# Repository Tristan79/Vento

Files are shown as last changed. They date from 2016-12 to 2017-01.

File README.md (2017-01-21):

# Vento

Wanna control you ventilation unit from your computer, tablet or phone? Can't sleep? Cuz the noise of the ventilation unit is too loud! Can't replace the unit because it is not yours, add Vento! The itho, duco, orcon, zehnder, storkair, berschenhoek: Arduino [MySensors 2.0](https://www.mysensors.org) perilex ventilation controller!

Manufactures air ventilation unit: itho, duco, orcon, zehnder, storkair, berschenhoek or ...

Price range parts: essential € 5 ~ full blown € 50

You need a MySensors gateway and a Smart Home Controller supporting MySensors like [Domoticz](www.domoticz.com)
Luckily if you have a raspberry Pi a gateway costs just 67 cents extra! [See this](https://www.domoticz.com/forum/viewtopic.php?t=14365&#p105148)

Contact <tristan@monkeycat.nl>!

## WARNING!

READ THE LICENSE FIRST! BE CAREFULL! 

## Other Nice Smarthome stuff!!

 * [iBrew](https://github.com/Tristan79/iBrew) iKettle, iKettle 2.0 and Smarter Coffee Interface
 * [iSamsungTV](https://github.com/Tristan79/iSamsungTV) the command line interface to Samsung TV series C, D, E, F and Blue Ray Disc Players with Smart Hub feature.
 * [Medisana Scale](https://github.com/keptenkurk/BS440) with [Domoticz](http://domoticz.com/) bridge to Medisana BS440, BS430,... weight scales.
 * [Xiaomi Mi Plant Sensor](https://github.com/Tristan79/miflora) with [Domoticz](http://domoticz.com/) bridge
 * [HUE Hack](https://github.com/Tristan79/HUEHack) Soft Link Button for HUE Bridge (& rooting the bridge & enable WiFi!)

## Vento!

Domoticz

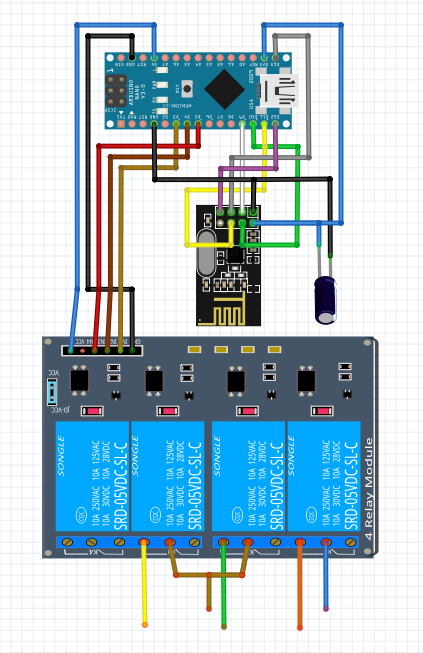
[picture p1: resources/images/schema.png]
Scheme3


Choose between Vento L1 and Vento L3 depending on your model.

## Vento L1

__Make sure your unit has the following specification__

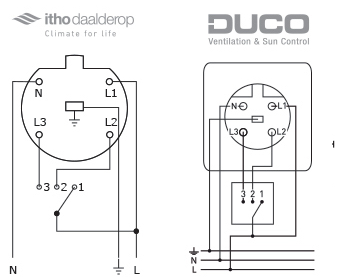
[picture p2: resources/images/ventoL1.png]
Specs2


You can cut open the existing cable and use that! Or use extra perilex plugs!

 * Blue: N power socket
 * Brown: L1 power socket
 * Orange: N ventilation unit
 * Yellow: L3 ventilation unit
 * Green: L2 ventilation unit
 * L2 & L3 power socket terminated
 * L1 & Ground directly connected

```
Power Socket          Ventilation Unit
Ground ________________________ Ground
N  ____________ Relay 1 ____________ N
L1 ________________________________ L1
L2 (T)      |___Relay 2 ___________ L2
L3 (T)      |__ Relay 3 ___________ L3
```

## Vento L3
__Make sure your unit has the following specification__

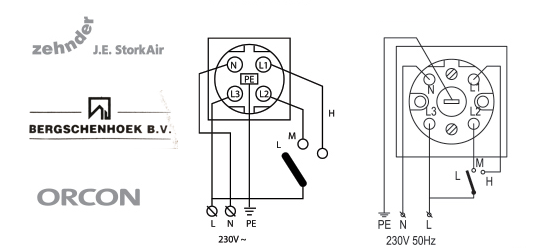
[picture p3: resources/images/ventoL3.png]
Specs3


You can cut open the existing cable and use that! Or use extra perilex plugs!

 * Blue: N power socket
 * Brown: L3 power socket
 * Orange: N ventilation unit
 * Yellow: L1 ventilation unit
 * Green: L2 ventilation unit
 * L1 & L2 power socket terminated
 * L3 & Ground directly connected

```
Power Socket          Ventilation Unit
Ground ________________________ Ground
N  ____________ Relay 1 ____________ N
L3 ________________________________ L3
L2 (T)      |___Relay 2 ___________ L2
L1 (T)      |__ Relay 3 ___________ L1
```

## Relay

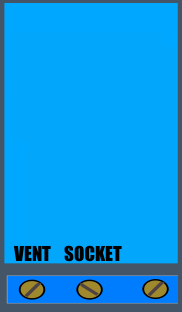
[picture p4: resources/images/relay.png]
Relay


## [Domoticz](www.domoticz.com)

## Showcase

Prototype!?

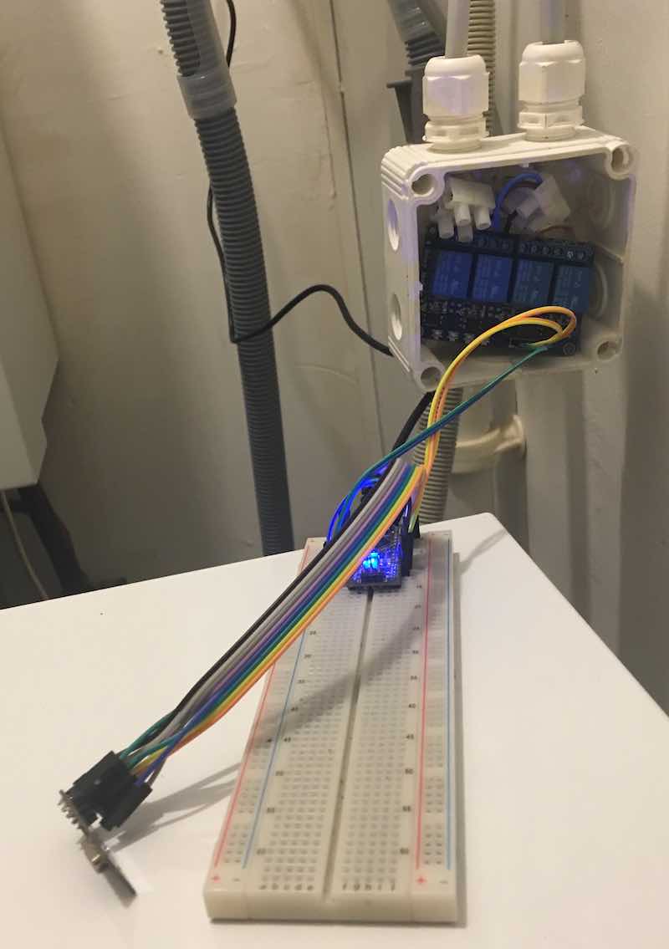
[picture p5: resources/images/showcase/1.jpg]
Showcase1


The unit...

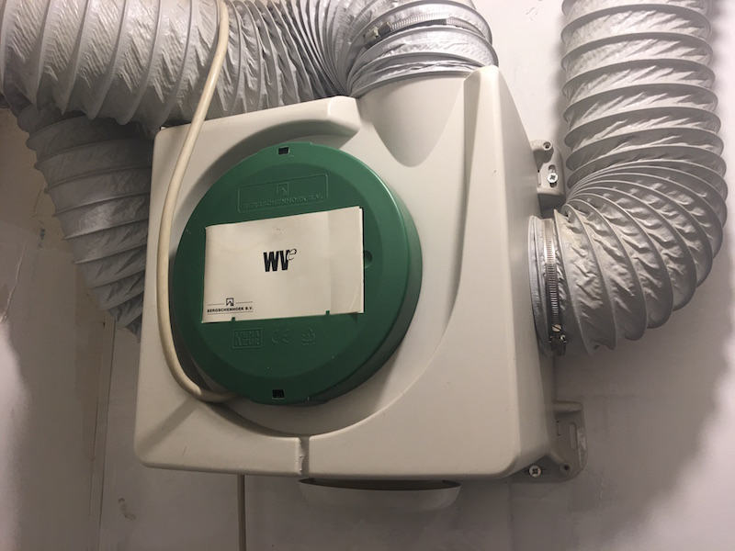
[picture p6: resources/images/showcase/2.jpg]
Showcase2


All connected!

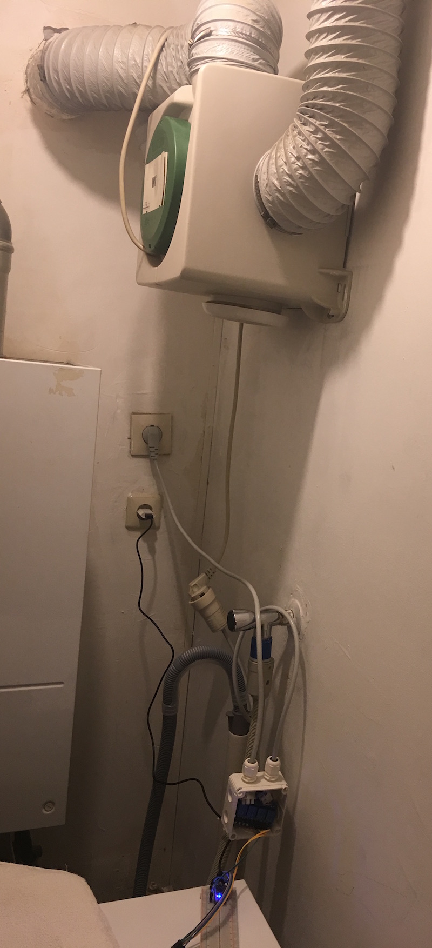
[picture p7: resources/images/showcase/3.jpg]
Showcase3


Assembled!

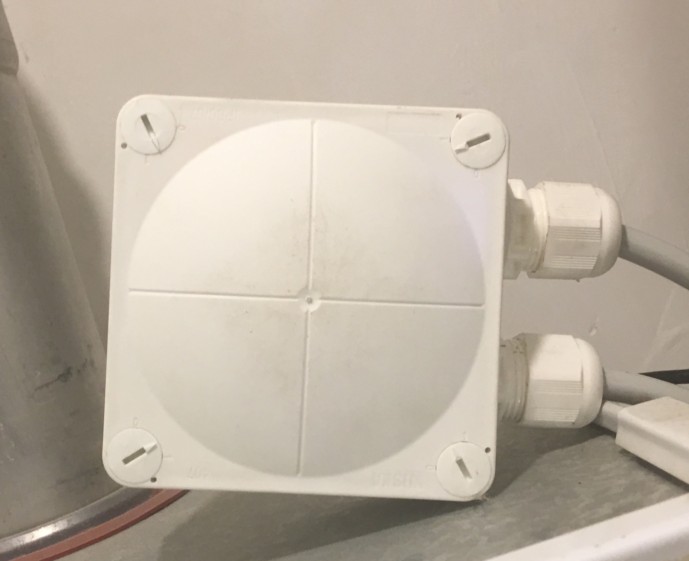
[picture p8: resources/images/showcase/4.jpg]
Showcase4


Photo's in the dark such that you really see the lights of Level 1, Level 2 and Level 3

Level1Level2Level3

## WARNING

Make sure you seperate the 5v wires and circuits from the 220v wires! That if one comes loose it will not touch any 5v stuff and burn the unit! I glued in a plastic seperator dividing the high wires and the rest of the stuff... 
 
## Parts, Shop & Prices 

Prices are snapshot 27 december 2016:

__Essential__
 * € 1.72 [Relay 4x](https://nl.aliexpress.com/item/1pcs-lot-4-channel-relay-module-4-channel-relay-control-board-with-optocoupler-Relay-Output-4/32325541816.html)
 * € 2.42 [Arduino Nano v3 ATmega328](https://nl.aliexpress.com/item/Free-Shipping-1PCS-LOT-For-arduino-Nano-3-0-Atmel-ATmega328-Mini-USB-Board/32773364249.html)
 * € 0.67 [Radio NRF24L01+](https://nl.aliexpress.com/item/1pcs-lot-Black-nrf24l01-wireless-module-24l01-2-4g-wireless-module-black-diamond-free-shipping/32649100793.html)
 * € 0.59 [Dupond male to male wires](https://nl.aliexpress.com/item/40pcs-lot-10cm-2-54mm-1pin-Female-to-Male-jumper-wire-Dupont-cable/32566136519.html)
 * € 0.66 [Plastic Barrier Terminal Blok](https://nl.aliexpress.com/item/10A-2-Position-Wire-Connector-Plastic-Barrier-Terminal-Block-High-Quality/32714811508.html)
 * € 0.37 [4.7µ - 47µF Capacitor](https://nl.aliexpress.com/item/Free-shipping-100pcs-47UF-50V-Electrolytic-Capacitor-50V-47UF-Aluminum-Electrolytic-Capacitor-6X12mm/32316099910.html)
 * € Total 6,43
 
__Perilex & Box__
 * € 7.28 [Perilex plug male & wire](http://www.bengshop.nl/detailitem.php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)
 * € 11.61 [Perilex plug female](http://www.bengshop.nl/detailitem.php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)
 * € 3.51 [Box](http://www.bengshop.nl/detailitem.php?sess=&shop=5&lang=nl&art_id=14614105) 
 * € 8.50 Delivery cost bengshop 
 * Total € 30,90  

__Power__
 * € 7.79 [USB Power Adapter](https://www.allekabels.nl/usb-lader/4508/1196134/usb-thuislader-1000-ma.html)
 * € 3,95 Delivery cost allekabels
 * € 1.26 [Mini USB cable](https://nl.aliexpress.com/item/White-1m-MiNi-USB-to-USB-2-0-Cable-Data-Sync-Charge-Cable-for-MP3-MP4/32622398168.html)
 * Total € 12,36
 
And isolation tape or soldering stuff and screwdrivers :-)

Please search yourself for the lowest prices!

Price Range € 6.43 - € 50,33

## [Fritzing](http://fritzing.org)
Fritzing [Relay 4 Channel](https://timgolisch.wordpress.com/2015/09/12/fritzing-4-channel-relay-part/) part

## License

Copyright (c) 2017, Tristan Crispijn
All rights reserved.

Redistribution and use in source and binary forms, with or without modification, are permitted provided that the following conditions are met:

1. Redistributions of source code must retain the above copyright notice, this list of conditions and the following disclaimer.

2. Redistributions in binary form must reproduce the above copyright notice, this list of conditions and the following disclaimer in the documentation and/or other materials provided with the distribution.

3. You may not use source, binary forms or derivative work, with or without modification, for commercial purposes. 

4. Written consent of the Vento creator Tristan Crispijn with original authentic signature on paper.

THIS SOFTWARE IS PROVIDED BY THE COPYRIGHT HOLDERS AND CONTRIBUTORS "AS IS" AND ANY EXPRESS OR IMPLIED WARRANTIES, INCLUDING, BUT NOT LIMITED TO, THE IMPLIED WARRANTIES OF MERCHANTABILITY AND FITNESS FOR A PARTICULAR PURPOSE ARE DISCLAIMED. IN NO EVENT SHALL THE COPYRIGHT HOLDER OR CONTRIBUTORS BE LIABLE FOR ANY DIRECT, INDIRECT, INCIDENTAL, SPECIAL, EXEMPLARY, OR CONSEQUENTIAL DAMAGES (INCLUDING, BUT NOT LIMITED TO, PROCUREMENT OF SUBSTITUTE GOODS OR SERVICES; LOSS OF USE, DATA, OR PROFITS; OR BUSINESS INTERRUPTION) HOWEVER CAUSED AND ON ANY THEORY OF LIABILITY, WHETHER IN CONTRACT, STRICT LIABILITY, OR TORT (INCLUDING NEGLIGENCE OR OTHERWISE) ARISING IN ANY WAY OUT OF THE USE OF THIS SOFTWARE, EVEN IF ADVISED OF THE POSSIBILITY OF SUCH DAMAGE. YOU AGREE TO NOT USE THIS SOFTWARE IN ANY WAY.

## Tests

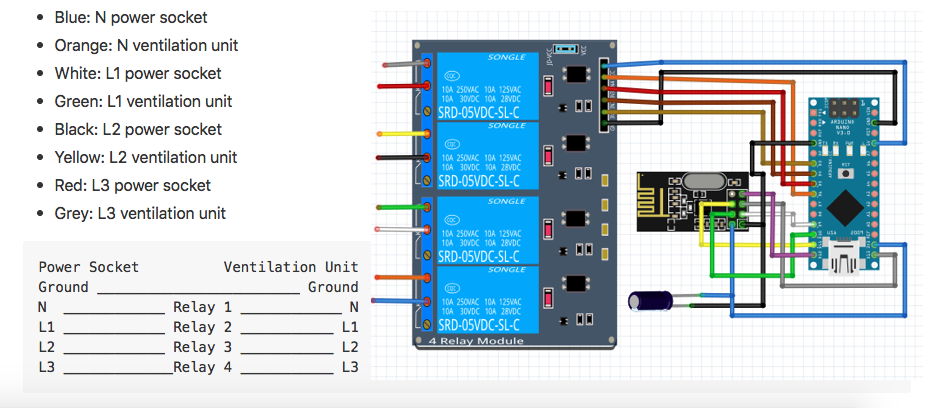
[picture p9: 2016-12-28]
resources/test/test.png

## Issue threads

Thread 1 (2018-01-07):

Relay 1 connection question

azhiltsov, 2018-01-07:
I am wondering why did you connect Relay 1 in the "N" circuit, while for safety it should be on L3 for "Vento L3" or on L1 for "Vento L1".  Was there any particular reason for that?

Tristan79, 2018-01-15:
Yeah, you are right. It would be much safer to cut all connections, if you want to power it off completely. No reason, other than I did not think it through, and just cut N instead of all.

azhiltsov, 2018-01-17:
I was asking mainly because I faced issue with relay got stuck in "ON" position at "MAX" speed and I thought that might be you've done this on purpose. Probably when it switches to the max it discharges capacitor in extraction fan. I might try to change the logic to not keep L1/L3 always connected, but switch it off instead, when changing to higher power.

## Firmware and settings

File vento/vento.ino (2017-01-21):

// Vento (c) 2017 Tristan Crispijn
// See LICENSE!

//#define MY_DEBUG
#define MY_RADIO_NRF24
#define MY_REPEATER_FEATURE

#include <MySensors.h>

#define RELAY_OFF 1
#define RELAY_ON 0

#define RELAY_POWER 3
#define RELAY_LEVEL2 4
#define RELAY_LEVEL3 5

#define MYSENSOR_POWER 1
#define MYSENSOR_LEVEL1 2
#define MYSENSOR_LEVEL2 3
#define MYSENSOR_LEVEL3 4
#define MYSENSOR_OFF 0
#define MYSENSOR_ON 1

#define LEVEL1 1
#define LEVEL2 2
#define LEVEL3 3

#define MEM_POWER 1
#define MEM_LEVEL 2

// Delay for switching back on when received off when level already selected
#define DELAY 500

bool power;
int level;
bool level1 = false;
bool level2 = false;
bool level3 = false;

#ifdef MY_DEBUG
void debug() {
  Serial.print("Power: ");
  Serial.print(power);
  Serial.print(", Level: ");
  Serial.print(level);
  Serial.print(", Level1: ");
  Serial.print(level1);
  Serial.print(", Level2: ");
  Serial.print(level2);
  Serial.print(", Level3: ");
  Serial.println(level3);
}
#endif

void before() {
  // Load power state and set relay
  power =  loadState(MEM_POWER);
  pinMode(RELAY_POWER, OUTPUT);
  digitalWrite(RELAY_POWER, power ? RELAY_ON : RELAY_OFF);

  // Disable Level1 & Level2
  pinMode(RELAY_LEVEL2, OUTPUT);
  digitalWrite(RELAY_LEVEL2, RELAY_OFF);
  pinMode(RELAY_LEVEL3, OUTPUT);
  digitalWrite(RELAY_LEVEL3, RELAY_OFF);

  // Load levels and set relay if power
  level =  loadState(MEM_LEVEL);
  if (level != LEVEL2 and level != LEVEL3) {
    level1 = true;
    level = LEVEL1;
  }
  if (level == LEVEL2) {
    level2 = true;
    if (power) digitalWrite(RELAY_LEVEL2, RELAY_ON);
  }
  if (level == LEVEL3) {
    level3 = true;
    if (power) digitalWrite(RELAY_LEVEL3, RELAY_ON);
  }
#ifdef MY_DEBUG
  debug();
#endif
}

void sendlevel(int level, bool state) {
  send(MyMessage(level, S_BINARY).set(state == HIGH));
#ifdef MY_DEBUG
  Serial.print("Sending: Sensor: ");
  Serial.print(level);
  Serial.print(", state: ");
  Serial.println(state);
#endif
}

void sendpower() {
  send(MyMessage(MYSENSOR_POWER, S_BINARY).set(power == HIGH));
}

void setup() {
  sendlevel(MYSENSOR_LEVEL1, level1);
  sendlevel(MYSENSOR_LEVEL2, level2);
  sendlevel(MYSENSOR_LEVEL3, level3);
  sendpower();
}

void presentation() {
  sendSketchInfo("Vento", "0.3.0");
  present(MYSENSOR_POWER, S_BINARY);
  present(MYSENSOR_LEVEL1, S_BINARY);
  present(MYSENSOR_LEVEL2, S_BINARY);
  present(MYSENSOR_LEVEL3, S_BINARY);
}

void loop() {
}

void receive(const MyMessage &message) {

  if (message.type == V_STATUS) {

    if (message.sensor == MYSENSOR_POWER) {

      // Switch power
      power = message.getBool();
      digitalWrite(RELAY_POWER, power ? RELAY_ON : RELAY_OFF);
      sendpower();
      saveState(MEM_POWER, power);

      // ...
      if (power) {
        if (level2) digitalWrite(RELAY_LEVEL2, RELAY_ON);
        if (level3) digitalWrite(RELAY_LEVEL3, RELAY_ON);
      } else {
        if (level2) digitalWrite(RELAY_LEVEL2, RELAY_OFF);
        if (level3) digitalWrite(RELAY_LEVEL3, RELAY_OFF);
      }
    }

    if (message.sensor == MYSENSOR_LEVEL1) {
      debug();
      if (level2) {
        level2 = false;
        sendlevel(MYSENSOR_LEVEL2, level2);
        if (power) digitalWrite(RELAY_LEVEL2, RELAY_OFF);
      }
      if (level3) {
        level3 = false;
        sendlevel(MYSENSOR_LEVEL3, level3);
        if (power) digitalWrite(RELAY_LEVEL3, RELAY_OFF);
      }
      if (not level1 || (level1 && MYSENSOR_OFF == message.getBool())) {
        if (MYSENSOR_OFF == message.getBool()) {
          delay(DELAY);
        }
        level1 = true;
        sendlevel(message.sensor, level1);
      }
      if (level != LEVEL1) {
        level = LEVEL1;
        saveState(MEM_LEVEL, level);
      }
    }

    if (message.sensor == MYSENSOR_LEVEL2) {
      debug();
      if (level1) {
        level1 = false;
        sendlevel(MYSENSOR_LEVEL1, level1);
      }
      if (level3) {
        level3 = false;
        sendlevel(MYSENSOR_LEVEL3, level3);
        if (power) digitalWrite(RELAY_LEVEL3, RELAY_OFF);
      }
      if (not level2 || (level2 && (MYSENSOR_OFF == message.getBool()))) {
        if (MYSENSOR_OFF == message.getBool()) {
          delay(DELAY);
        }
        level2 = true;
        sendlevel(message.sensor, level2);
        if (power) digitalWrite(RELAY_LEVEL2, RELAY_ON);
      }
      if (level != LEVEL2) {
        level = LEVEL2;
        saveState(MEM_LEVEL, level);
      }
    }

    if (message.sensor == MYSENSOR_LEVEL3) {
      debug();
      if (level1) {
        level1 = false;
        sendlevel(MYSENSOR_LEVEL1, level1);
      }
      if (level2) {
        level2 = false;
        sendlevel(MYSENSOR_LEVEL2, level2);
        if (power) digitalWrite(RELAY_LEVEL2, RELAY_OFF);
      }
      if (not level3 || (level3 && MYSENSOR_OFF == message.getBool())) {
        if (MYSENSOR_OFF == message.getBool()) {
          delay(DELAY);
        }
        level3 = true;
        sendlevel(message.sensor, level3);
        if (power) digitalWrite(RELAY_LEVEL3, RELAY_ON);
      }
      if (level != LEVEL3) {
        level = LEVEL3;
        saveState(MEM_LEVEL, level);
      }
    }

#ifdef MY_DEBUG
    Serial.print("Incoming change for sensor:");
    Serial.print(message.sensor);
    Serial.print(", New status: ");
    Serial.println(message.getBool());
    debug();
#endif
  }
}

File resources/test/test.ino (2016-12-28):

#define MY_DEBUG
#define MY_RADIO_NRF24
#define MY_REPEATER_FEATURE
#include <MySensors.h>
#define RELAY_1  3 
#define NUMBER_OF_RELAYS 4 
#define RELAY_ON 0  
#define RELAY_OFF 1 

// +1 for easy offset state[0] not used
int state[NUMBER_OF_RELAYS+1];

void before() { 
  for (int sensor = 1, pin = RELAY_1; sensor <= NUMBER_OF_RELAYS; sensor++, pin++) {
    pinMode(pin, OUTPUT);
    digitalWrite(pin, RELAY_OFF);
    state[sensor] = loadState(sensor);
  }
  digitalWrite(RELAY_1, state[1] ? RELAY_ON : RELAY_OFF);
  if (state[1]) {
    digitalWrite(RELAY_1 + 1, state[2] ? RELAY_ON : RELAY_OFF);
    digitalWrite(RELAY_1 + 2, state[3] ? RELAY_ON : RELAY_OFF);
    digitalWrite(RELAY_1 + 3, state[4] ? RELAY_ON : RELAY_OFF);   
  }
}

void setup() {
  for (int sensor = 1; sensor <= NUMBER_OF_RELAYS; sensor++) {
    send(MyMessage(sensor, S_BINARY).set(state[sensor]==HIGH));
  }
}

void presentation() {
  sendSketchInfo("Vento Switch", "0.2");
  for (int sensor = 1; sensor <= NUMBER_OF_RELAYS; sensor++) {
    present(sensor, S_BINARY);
  }
}

void loop() {
}

void go(int sensor,bool value) {
  if (sensor == 1) {
    digitalWrite(RELAY_1, value ? RELAY_ON : RELAY_OFF);
    if (not value && state[2]) digitalWrite(1 + RELAY_1, RELAY_OFF);
    if (not value && state[3]) digitalWrite(2 + RELAY_1, RELAY_OFF);
    if (not value && state[4]) digitalWrite(3 + RELAY_1, RELAY_OFF);      
    if (value && state[2]) digitalWrite(1 + RELAY_1, RELAY_ON);
    if (value && state[3]) digitalWrite(2 + RELAY_1, RELAY_ON);
    if (value && state[4]) digitalWrite(3 + RELAY_1, RELAY_ON);      
  } else {
    if (state[1]) {
        digitalWrite(sensor - 1 + RELAY_1, value ? RELAY_ON : RELAY_OFF);
    } 
  }
  send(MyMessage(sensor, S_BINARY).set(value==HIGH));  
  state[sensor] = value;
  saveState(sensor,value);
  Serial.println(state[sensor]);
}

void receive(const MyMessage &message) {
  if (message.type == V_STATUS) {
    if (message.sensor == 1) {
      go(1,message.getBool()); 
    }
    if (message.sensor == 2) {
      go(3,false);
      go(4,false);   
      go(2,true);
    }
    if (message.sensor == 3) {
      go(2,false);
      go(4,false);
      go(3,true);
    }
    if (message.sensor == 4) {
      go(2,false);
      go(3,false);
      go(4,true);
    }

    #ifdef MY_DEBUG
    Serial.print("Incoming change for sensor:");
    Serial.print(message.sensor);
    Serial.print(", New status: ");
    Serial.println(message.getBool());
    #endif
  }
}
